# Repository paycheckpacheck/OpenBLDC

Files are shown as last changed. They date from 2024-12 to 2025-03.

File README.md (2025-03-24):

## Members
Pacheck Nicholas, Electrical Engineering Student (2025)
pacheck@vt.edu

Eddie Prichard (Computer Engineering Alum)

New contributors:
Enrico
Colton

## Mentor
Pacheck Nicholas
Eddie Prichard

## Current Status
IN PROGRESS

## Project Overview

The goal specifications for this motor driver should be to drive a 40V 10A load per phase. 

This project provides Open Source Hardware and Firmware for a 3-Phase Brushless DC Motor Driver. It aims to be an educational platform for some basic Power Electrionics problems.

To understand how a BLDC motor works, we must understand how a DC motor works. Well, its pretty simple, we apply a voltage and the motor spins. What if we want to have speed control? 
Well, we must decrease the average coil voltage. We can use a variable power supply to do this, or we can do this with a swith mode driver which will apply a PWM to the motor coil, allowing us to modify the duty cycle to compute the average voltage on the coil. 

An N-Channel Inverter is used to take that low power PWM generated from the discrete-controller/microcontroller and use it to switch on and off the Powersupply directly.

Below is an image of the N-Channel Inverter Developed after expirmental trials using a breadboard:



In additon to the cooresponding schematic:


This N-channel inverter essentially connects the Switch Node (Output) to power, or to ground. To Connect the Switch Node to Power, you must activate the High-Side Fet and deactivate the Low-side Fet; vice versa to connect to ground. 

But whats stopping us from just hooking up an inverter and directly driving the Gates of the Fets using something like an OpAmp? Gate Capacitance! In reality, there are two conditions required for a MOSFET to turn on ( Surpassing the Gate-Source voltage (VGS)) which is ussually found in the datasheet, AND filling up the gate capacitor. In order for a MOSFET to have fast switching, we must put consideration into the gate capacitance. In the datasheet, there is ussually like an effective gate charge, which is the total amount of charge needed to fill up the gate capacitor, this charge also needs to be dumped into the gate quicly, since there is a high frequrncy switching and not doing it fast enough or not filling it up entirely will cause the MOSFET to not fully turn on. 

Hence introducing the need for a bootstrap capacitor and bootstrap diode. These two components work as a team; the bootstrap diode allows the bootstrap capacitor to charge through the VCC, while also inuring the charge doesnt leak back in the way it came in. Now, during the lowside cycle, the bootstrap capacitor is charged up such that when the

The board has footprints for the 3-pin THT MOSFET package or the D-PACK6 Mosfet footprint.

A BLDC motor driver is just 3 of these. 


Here is the schem for the driver below.


## Educational Value Added
This BLDC driver is made out of primitive components. Instead of using a chip or IC which contains the entire BLDC driver, this project provides eduational value with the constraint that everything must be primitive. The current sense is done using a differential instrumentation amplifer made with op amps. Transient voltage supression (TVS) diodes are placed at the switch node with clamp voltage at about 32volts

## Tasks

<!-- Your Text Here. You may work with your mentor on this later when they are assigned -->

## Design Decisions

<!-- Your Text Here. You may work with your mentor on this later when they are assigned -->

## Steps for Documenting Your Design Process

<!-- Your Text Here. You may work with your mentor on this later when they are assigned -->

## BOM + Component Cost

<!-- Your Text Here. You may work with your mentor on this later when they are assigned -->

## Timeline

<!-- Your Text Here. You may work with your mentor on this later when they are assigned -->

## Useful Links

<!-- Your Text Here. You may work with your mentor on this later when they are assigned -->

## Log

<!-- Your Text Here. You may work with your mentor on this later when they are assigned -->

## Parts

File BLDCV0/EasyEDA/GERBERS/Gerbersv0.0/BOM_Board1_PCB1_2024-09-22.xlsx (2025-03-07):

No. | Quantity | Comment | Designator | Footprint | Value | Manufacturer Part | Manufacturer | Supplier Part | Supplier
1 | 9 | 0Ω | C1,C7,C13,C15,C16,C20,C22,C23,C27 | C0603 | 0Ω | RMC060301%N | Tyohm(幸亚电阻) | C269698 | LCSC
2 | 6 | 10uF | C9,C10,C17,C18,C24,C25 | CAP-SMD_BD5.0-L5.3-W5.3-LS6.3-FD | 10uF | RST10UF50V016 | KNSCHA(科尼盛) | C4747971 | LCSC
3 | 6 | 1uF | C12,C14,C19,C21,C26,C28 | CAP-TH_L7.2-W2.5-P5.00-D0.6 | 1uF | SMEC334J100M2 | CHAMPION(全鹏) |  | LCSC
4 | 3 | .1uF | C33,C34,C35 | C0402 | .1uF
5 | 1 | 500nF | C36 | C0603 | 500nF
6 | 1 | 1uF | C37 | CAP-SMD_BD5.0-L5.3-W5.3-LS6.3-FD | 1uF
7 | 1 | 200nF | C38 | C0603 | 200nF
8 | 1 | .1uF | C39 | CAP-SMD_BD5.0-L5.3-W5.3-LS6.3-FD | .1uF
9 | 3 | 1N5819WS | D1,D3,D5 | SOD-323_L1.8-W1.3-LS2.5-RD |  | 1N5819WS | Hottech(合科泰) | C191023 | LCSC
10 | 4 | P6SMB6.8CA/TR13 | D2,D4,D6,D8 | SMB_L4.6-W3.6-LS5.3-BI |  | P6SMB6.8CA/TR13 | Brightking(君耀电子) | C78395 | LCSC
11 | 1 | 1N4007 | D7 | DO-41_BD2.4-L4.7-P8.70-D0.9-RD
12 | 1 | HDR-F-2.54_2x2 | DGHTRPWR | HDR-TH_4P-P2.54-V-F-R2-C2-S2.54
13 | 2 | 2.54-1*6P母 | DRV_IN,SenseOut | HDR-TH_6P-P2.54-V-F |  | 2.54-1*6P母 | BOOMELE(博穆精密) | C40877 | LCSC
14 | 3 | HDR-M_2.54_1x4P | H1,H2,H3 | HDR-TH_4P-P2.54-V-M
15 | 1 | 1729128 | PWR_IN | CONN-TH_2P-P5.08 |  | 1729128 | Phoenix Contact(菲尼克斯) | C91153 | LCSC
16 | 6 | IRF2804STRL7PP | Q1,Q2,Q3,Q4,Q5,Q6 | D2PAK-7_L10.6-W9.6-P1.27-LS15.9-BR |  | IRF2804STRL7PP | Infineon(英飞凌) | C459950 | LCSC
17 | 3 | 5mΩ | R7,R10,R13 | R2512 | 5mΩ | PA2512FKF7W0R005E | YAGEO(国巨) | C309526 | LCSC
18 | 6 | 10kΩ | R8,R9,R11,R12,R14,R15 | RES-TH_BD3.3-L9.0-P13.00-D0.6 | 10kΩ
19 | 1 | 720 | R16 | RES-TH_BD3.3-L9.0-P13.00-D0.6 | 720
20 | 1 | 240 | R17 | RES-TH_BD3.3-L9.0-P13.00-D0.6 | 240
21 | 6 | 0Ω | RHS1,RHS2,RHS3,RLS1,RLS2,RLS3 | R1210 | 0Ω | SCR1210F0R | VO(翔胜) | C3017387 | LCSC
22 | 3 | IR2104PBF | U1,U2,U3 | DIP-8_L9.9-W6.6-P2.54-LS7.62-BL |  | IR2104PBF | Infineon(英飞凌) | C2959 | LCSC
23 | 3 | INA180A3IDBVT | U4,U5,U6 | SOT-23-5_L2.9-W1.6-P0.95-LS2.8-TL |  | INA180A3IDBVT | TI(德州仪器) | C2877844 | LCSC
24 | 1 | LM317T | U9 | TO-220-3_L10.0-W4.6-P2.54-L |  | LM317T | Siproin(上海矽朋) | C5444279 | LCSC
25 | 1 | XY636-7.62-3P | U10 | CONN-TH_XY636-7.62-3P |  | XY636-7.62-3P | XINLAIYA(新莱亚) | C880593 | LCSC

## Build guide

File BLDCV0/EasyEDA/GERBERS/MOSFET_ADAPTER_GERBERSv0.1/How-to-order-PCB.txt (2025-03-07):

How to Order PCB

Please refer to:
https://prodocs.easyeda.com/en/pcb/order-order-pcb/index.html

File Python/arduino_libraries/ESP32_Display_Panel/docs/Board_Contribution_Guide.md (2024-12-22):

# Board Contribution Guide

1. Newly added development boards must ensure the hardware schematics are open-source. Please provide a link or file.
2. This library currently only supports the APIs provided in ESP-IDF. It does not support other Arduino library APIs, such as Wire.

**Note**:
1. It is recommended to use the vscode + Arduino CLI development environment.
2. Pull the ESP32_Display_Panel repository into the Arduino library directory before making modifications.
3. The project uses pre-commit to enforce commit standards. It is recommended to install the pre-commit library before committing using the following command:

```
pip3 install pre-commit && pre-commit install
```

## Modification Content

Using the adaption of the [`M5Stack M5DIAL`](https://github.com/esp-arduino-libs/ESP32_Display_Panel/commit/1886c668468626b9dd2ae975f7db12df5413378e) development board as an example. Following this guide, changes below will be made under the project:

```
| -ESP32_Display_Panel
   | -src
      | -board
         | -m5stack                    [A]
            | -M5DIAL.h                [A]
         | -ESP_PanelBoard             [M]
         | -README.md                  [M]
      | -ESP_PanelVersions.h           [M]
   | -CHANGELOG.md                     [M]
   | -ESP_Panel_Board_Custom.h
   | -ESP_Panel_Board_Supported.h      [M]
   | -library.properties               [M]
   | -README_CN.md                     [M]
   | -README.md                        [M]
```
Note: [A] stands for 'append' and [M] stands for 'modify'

## Modification Process

Using the adaption of `M5Stack M5DIAL` as an example, follow these steps to modify the relevant files:

1. **[M]** *[ESP_Panel_Board_Supported.h](../ESP_Panel_Board_Supported.h)*: Add a macro for the new development board, such as `BOARD_M5STACK_M5DIAL`. Ensure the macro is in uppercase. Include the manufacturer's name and link, as well as the target development board's link.
2. **[A]** *[src/board/m5stack/M5DIAL.h](../src/board/m5stack/M5DIAL.h)*: Use the *ESP_Panel_Board_Custom.h* file in the root directory as a template to create a new configuration header file for the development board. Follow the naming conventions of existing development boards.
3. **[M]** *[src/board/ESP_PanelBoard.h](../src/board/ESP_PanelBoard.h)*: Add the macro check for the new development board by referring to the existing boards in the file, and modify the file to use the correct header file for this development board.

   **Note**: At this point, you can verify the above steps:

      - Choose an example, such as *[examples/Panel/PanelTest](../examples/Panel/PanelTest/)*.
      - modify the macro `ESP_PANEL_USE_SUPPORTED_BOARD` to enable this header file. Define the development board macro, such as `BOARD_M5STACK_M5DIAL`, to enable the new header file *[src/board/m5stack/M5DIAL.h](../src/board/m5stack/M5DIAL.h)*.
      - Verify the example's ino file. If successful, proceed to the following steps.

4. **[M]** *[src/board/m5stack/M5DIAL.h](../src/board/m5stack/M5DIAL.h)*: Modify the configuration header file for the new development board:
   - Review the hardware schematics of the development board, focusing on the BUS type used for the LCD screen, the LCD driver name, the BUS type used for touch, the touch driver name, and the chip pin numbers used for each interface of the LCD and touch.
   - The best practice is to first get the screen working, then work on the touch functionality.
   - If the new development board's driver is compatible with an existing driver, there is no need to add a new driver. Simply note in the comments that this driver is compatible with an existing one and use the existing driver.
   - If the driver used by the new development board is not compatible with existing drivers or has other special configurations, you can achieve this by modifying the macro functions at the end of the new development board's configuration header file, such as `ESP_PANEL_BEGIN_BACKLIGHT_START_FUNCTION`, `ESP_PANEL_BEGIN_END_FUNCTION`, etc. Refer to *[src/board/espressif/ESP32_S3_BOX_3.h](../src/board/espressif/ESP32_S3_BOX_3.h)* or *[src/board/m5stack/M5DIAL.h](../src/board/m5stack/M5DIAL.h)* for specific implementations.
   - Run examples other than *[examples/LCD](../examples/LCD/)* and *[examples/Touch](../examples/Touch/)*, and continuously adjust the configuration header file to ensure correct settings.

5. **[M]** *[ESP_Panel_Board_Supported](../ESP_Panel_Board_Supported.h)*, *[library.properties](../library.properties)*, *[docs/Board_Instructions.md](../docs/Board_Instructions.md)*, *[README_CN.md](../README_CN.md)*, *[README.md](../README.md)*: Update the supported development boards information in these files.
6. **[M]** *[docs/Board_Instructions.md](../docs/Board_Instructions.md)*: Update the recommended configuration for the new development board.
7. **[M]** *[src/ESP_PanelVersions.h](../src/ESP_PanelVersions.h)*: Ensure that the version under `Library Version` should be ahead of the latest tag version in terms of the tag version; when changes occur to *[ESP_Panel_Board_Custom.h](../ESP_Panel_Board_Custom.h)*, *[ESP_Panel_Board_Supported.h](../ESP_Panel_Board_Supported.h)*, and *[ESP_Panel_Conf.h](../ESP_Panel_Conf.h)* in the root directory, ensure that the version number at the end of the corresponding file and at the beginging of *[src/ESP_PanelVersions.h](../src/ESP_PanelVersions.h)* should be ahead of the latest tag version in terms of the minor version.
8. **[M]** *[CHANGELOG.md](../CHANGELOG.md)*: Update the changelog.

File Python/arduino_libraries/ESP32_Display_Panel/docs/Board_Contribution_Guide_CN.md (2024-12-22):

# 开发板贡献指南

1. 新添加的开发板需要确保硬件原理图开源，需要提供链接或文件。
2. 该库目前仅支持 ESP-IDF 提供的 API，不支持其他 Arduino 库 API，如 Wire。

**注意**：
1. 推荐使用 vscode + Arduino CLI 开发环境。
2. 在进行修改之前，将 ESP32_Display_Panel 仓库拉入 Arduino 库目录中。
3. 项目使用 pre-commit 来规范提交内容，因此建议在提交之前安装 pre-commit 库，使用以下命令：

```
pip3 install pre-commit && pre-commit install
```

## 需修改内容

以适配 [`M5Stack M5DIAL`](https://github.com/esp-arduino-libs/ESP32_Display_Panel/commit/1886c668468626b9dd2ae975f7db12df5413378e) 开发板为例。按照本指南，以下更改将在项目中进行：

```
| -ESP32_Display_Panel
   | -src
      | -board
         | -m5stack                    [A]
            | -M5DIAL.h                [A]
         | -ESP_PanelBoard             [M]
         | -README.md                  [M]
      | -ESP_PanelVersions.h           [M]
   | -CHANGELOG.md                     [M]
   | -ESP_Panel_Board_Custom.h
   | -ESP_Panel_Board_Supported.h      [M]
   | -library.properties               [M]
   | -README_CN.md                     [M]
   | -README.md                        [M]
```
注：[A] 代表 '添加'，[M] 代表 '修改'

## 各文件修改流程

以适配 `M5Stack M5DIAL` 为例，按照以下步骤修改相关文件：

1. **[M]** *[ESP_Panel_Board_Supported.h](../ESP_Panel_Board_Supported.h)*：为新开发板添加一个宏，例如 `BOARD_M5STACK_M5DIAL`。命名时注意宏名大写。注意附上开发板制造商的名称和链接，以及目标开发板的链接。
2. **[A]** *[src/board/m5stack/M5DIAL.h](../src/board/m5stack/M5DIAL.h)*：使用根目录中的 *ESP_Panel_Board_Custom.h* 文件作为模板，为开发板创建一个新的配置头文件。文件命名请参考已有开发板。
3. **[M]** *[src/board/ESP_PanelBoard.h](../src/board/ESP_PanelBoard.h)*：参照文件中其他开发板的写法，添加新开发板的宏名判断，并注意修改此开发板所使用的头文件。

   **注意**：此时，可以验证上述步骤：

      - 选择一个示例，例如 *[examples/Panel/PanelTest](../examples/Panel/PanelTest/)*。
      - 修改宏 `ESP_PANEL_USE_SUPPORTED_BOARD` 以启用此头文件。定义开发板宏，例如 `BOARD_M5STACK_M5DIAL`，以启用新的头文件 *[src/board/m5stack/M5DIAL.h](../src/board/m5stack/M5DIAL.h)*。
      - 验证示例的 ino 文件。如果成功，继续后续步骤。

4. **[M]** *[src/board/m5stack/M5DIAL.h](../src/board/m5stack/M5DIAL.h)*：修改新开发板的配置头文件：
   - 审查开发板的硬件原理图，重点关注LCD 屏幕所使用 BUS 类型、 LCD 驱动名、touch 所使用 BUS 类型、touch 驱动名，以及 LCD 和 touch 各接口所使用的芯片管脚号。
   - 修改技巧是先亮屏再 touch。
   - 如果新开发板的驱动程序与现有驱动程序兼容，则无需添加新驱动程序。只需在注释中注明该驱动程序与现有驱动程序兼容，并使用现有驱动程序。
   - 如果新开发板使用的驱动程序与现有驱动程序不兼容或有其他特殊配置，可以通过修改新开发板配置头文件末尾的宏函数来实现，例如 `ESP_PANEL_BEGIN_BACKLIGHT_START_FUNCTION`、`ESP_PANEL_BEGIN_END_FUNCTION` 等。具体实现请参考 *[src/board/espressif/ESP32_S3_BOX_3.h](../src/board/espressif/ESP32_S3_BOX_3.h)* 或 *[src/board/m5stack/M5DIAL.h](../src/board/m5stack/M5DIAL.h)*。
   - 运行除 *[examples/LCD](../examples/LCD/)* 和 *[examples/Touch](../examples/Touch/)* 以外的示例，并不断调整配置头文件以确保设置正确。

5. **[M]** *[ESP_Panel_Board_Supported](../ESP_Panel_Board_Supported.h)*、*[library.properties](../library.properties)*、*[docs/Board_Instructions.md](../docs/Board_Instructions.md)*、*[README_CN.md](../README_CN.md)*、*[README.md](../README.md)*：更新上述文件中“已支持开发板”说明。
6. **[M]** *[docs/Board_Instructions.md](../docs/Board_Instructions.md)*：更新新开发板的推荐配置。
7. **[M]** *[src/ESP_PanelVersions.h](../src/ESP_PanelVersions.h)*：确保 `Library Version` 下的版本应小版本领先于最新 tag 版本。当根目录下的 *[ESP_Panel_Board_Custom.h](../ESP_Panel_Board_Custom.h)*、*[ESP_Panel_Board_Supported.h](../ESP_Panel_Board_Supported.h)* 和 *[ESP_Panel_Conf.h](../ESP_Panel_Conf.h)* 发生变化时，相应文件末尾和 *[src/ESP_PanelVersions.h](../src/ESP_PanelVersions.h)* 开头的版本号应中版本领先于最新 tag 版本。
8. **[M]** *[CHANGELOG.md](../CHANGELOG.md)*：更新变更日志。

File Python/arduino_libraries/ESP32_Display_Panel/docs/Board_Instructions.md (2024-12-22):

# Board Instructions

## Internal Supported Development Boards

### [Espressif](https://www.espressif.com/en/products/devkits)

| **Picture** | **Name** | **LCD Bus** | **LCD Controller** | **LCD resolution** | **Touch Bus** | **Touch Controller** |
| :---: | :---: | :---: | :---: | :---: | :---: | :---: |
|  | [ESP32-C3-LCDkit](https://docs.espressif.com/projects/esp-dev-kits/en/latest/esp32c3/esp32-c3-lcdkit/index.html) | SPI | GC9A01 | 240x240 | - | - |
|  | [ESP32-S3-BOX](https://github.com/espressif/esp-box/tree/master) | SPI | ILI9342 | 320x240 | I2C | TT21100 |
|  | [ESP32-S3-BOX-3 & ESP32-S3-BOX-3B](https://github.com/espressif/esp-box/tree/master) | SPI | ILI9342 | 320x240 | I2C | GT911 |
|  | [ESP32-S3-BOX-3(beta)](https://github.com/espressif/esp-box/tree/c4c954888e11250423f083df0067d99e22d59fbe) | SPI | ILI9342 | 320x240 | I2C | TT21100 |
|  | [ESP32-S3-BOX-Lite](https://github.com/espressif/esp-box/tree/master) | SPI | ST7789 | 320x240 | - | - |
|  | [ESP32-S3-EYE](https://github.com/espressif/esp-who/blob/master/docs/en/get-started/ESP32-S3-EYE_Getting_Started_Guide.md) | SPI | ST7789 | 240x240 | - | - |
|  | [ESP32-S3-Korvo-2](https://docs.espressif.com/projects/esp-adf/en/latest/design-guide/dev-boards/user-guide-esp32-s3-korvo-2.html) | SPI | ILI9342 | 320x240 | I2C | TT21100 |
|  | [ESP32-S3-LCD-EV-Board](https://docs.espressif.com/projects/esp-dev-kits/en/latest/esp32s3/esp32-s3-lcd-ev-board/index.html) | 3-wire SPI + RGB | GC9503 | 480x480 | I2C | FT5x06 |
|  | [ESP32-S3-LCD-EV-Board-2](https://docs.espressif.com/projects/esp-dev-kits/en/latest/esp32s3/esp32-s3-lcd-ev-board/index.html) | RGB | ST7262E43 | 800x480 | I2C | GT1151 |
|  | [ESP32-S3-USB-OTG](https://docs.espressif.com/projects/esp-dev-kits/en/latest/esp32s3/esp32-s3-usb-otg/index.html) | SPI | ST7789 | 240x240 | - | - |

### [Elecrow](https://www.elecrow.com/)

| **Picture** | **Name** | **LCD Bus** | **LCD Controller** | **LCD resolution** | **Touch Bus** | **Touch Controller** |
| :---: | :---: | :---: | :---: | :---: | :---: | :---: |
|  | [CrowPanel 7.0"](https://www.elecrow.com/esp32-display-7-inch-hmi-display-rgb-tft-lcd-touch-screen-support-lvgl.html) | RGB | EK9716BD3 & EK73002ACGB | 800x480 | I2C | GT911 |

### [M5Stack](https://m5stack.com/)

| **Picture** | **Name** | **LCD Bus** | **LCD Controller** | **LCD resolution** | **Touch Bus** | **Touch Controller** |
| --- | --- | --- | --- | --- | --- | --- |
|  | [M5STACK_M5CORE2](https://docs.m5stack.com/en/core/core2) | SPI | ILI9342C | 320x240 | I2C | FT6336U |
|  | [M5STACK_M5DIAL](https://docs.m5stack.com/en/core/M5Dial) | SPI | GC9A01 | 240x240 | I2C | FT5x06 |
|  | [M5STACK_M5CORES3](https://docs.m5stack.com/en/core/CoreS3) | SPI | ILI9342C | 320x240 | I2C | FT6336U |

### [Shenzhen Jingcai Intelligent](https://www.displaysmodule.com/)

| **Picture** | **Name** | **LCD Bus** | **LCD Controller** | **LCD resolution** | **Touch Bus** | **Touch Controller** |
| :---: | :---: | :---: | :---: | :---: | :---: | :---: |
| [](https://www.displaysmodule.com/sale-41828962-experience-the-power-of-the-esp32-display-module-sku-esp32-4848s040c-i-y-3.html) | [ESP32-4848S040C_I_Y_3](http://pan.jczn1688.com/directlink/1/ESP32%20module/4.0inch_ESP32-4848S040.zip) | 3-wire SPI + RGB | ST7701 | 480x480 | I2C | GT911 |

## [Waveshare](https://www.waveshare.com/)

| **Picture** | **Name** | **LCD Bus** | **LCD Controller** | **LCD resolution** | **Touch Bus** | **Touch Controller** |
| :---: | :---: | :---: | :---: | --- | :---: | :---: |
|  | [ESP32-S3-Touch-LCD-4.3](https://www.waveshare.com/esp32-s3-touch-lcd-4.3.htm) | RGB | ST7262 | 800x480 | I2C | GT911 |

## Recommended Configurations in the Arduino IDE

Below are recommended configurations for developing GUI applications on different development boards. These settings can be adjusted according to specific requirements, and users can navigate to the `Tools` menu in the Arduino IDE to configure the following settings.

| Supported Boards | Selected Board |  PSRAM | Flash Mode | Flash Size | USB CDC On Boot | Partition Scheme |
| :---: | :---: | :---: | :---: | :---: | :---: | :---: |
| ESP32-C3-LCDkit | ESP32C3 Dev Module | Disabled | QIO | 4MB (32Mb) | Enabled | Default 4MB with spiffs |
| ESP32-S3-BOX | ESP32-S3-BOX | - | - | - | - | 16M Flash (3MB) |
| ESP32-S3-BOX-3 & ESP32-S3-BOX-3B | ESP32S3 Dev Module | OPI | QIO 80MHz  | 16MB | Enabled | 16M Flash (3MB) |
| ESP32-S3-BOX-3(beta) | ESP32S3 Dev Module | OPI | QIO 80MHz  | 16MB | Enabled | 16M Flash (3MB) |
| ESP32-S3-BOX-Lite | ESP32-S3-BOX | - | - | - | - | 16M Flash (3MB) |
| ESP32-S3-EYE | ESP32S3 Dev Module | OPI | QIO 80MHz  | 8MB | Enabled | 8M with spiffs |
| ESP32-S3-Korvo-2 | ESP32S3 Dev Module | OPI | QIO 80MHz  | 16MB | Disabled | 16M Flash (3MB) |
| ESP32-S3-LCD-EV-Board | ESP32S3 Dev Module | OPI | QIO 80MHz  | 16MB | **See Note 1**  | 16M Flash (3MB) |
| ESP32-S3-LCD-EV-Board-2 | ESP32S3 Dev Module | OPI | QIO 80MHz  | 16MB | **See Note 1**  | 16M Flash (3MB) |
| ESP32-S3-USB-OTG |  ESP32-S3-USB-OTG  | - | - | - | - | 8M with spiffs |
| M5STACK-M5CORE2 | M5Stack-Core2 | Enabled  | - | - | - | Default |
| M5STACK-M5DIAL | ESP32S3 Dev Module | OPI | QIO 80MHz  | 8MB | Disabled | Default |
| M5STACK-M5CORES3 | ESP32S3 Dev Module | OPI | QIO 80MHz  | 16MB | Enabled | Default 4MB with spiffs |
| ESP32-4848S040C_I_Y_3 | ESP32S3 Dev Module | OPI | QIO 80MHz  | 16MB | Disabled | 16M Flash (3MB) |
| ElecrowCrowPanel 7.0" | ESP32S3 Dev Module | OPI | QIO 80MHz  | 4MB | Disabled | Huge App (3MB) |
| Waveshare-ESP32-S3-Touch-LCD-4.3 | ESP32S3 Dev Module | OPI | QIO 80MHz  | 8MB | Disabled | 8M with spiffs |

**Notes:**

1. Enable or disable `USB CDC On Boot` based on the type of port used:

   * Disable this configuration if using **UART** port; enable it if using **USB** port.
   * If this configuration differs from previous flashing, first enable `Erase All Flash Before Sketch Upload`, then it can be disabled after flashing.
   * If this configuration does not match the actual port type, it will prevent the development board from printing serial logs correctly.

2. To view more output logs, set `Core Debug Level` to `Info` or a lower level.
3. If the predefined partition schemes provided by ESP32 do not meet the requirements, users can also select `Custom` in the "Partition Scheme" and create a custom partition table file `Custom.csv` in the `hardware/esp32/3.x.x/tools/partitions` directory under the [arduino-esp32 installation directory](#where-are-the-installation-directory-for-arduino-esp32-and-the-sdk-located). For detailed information on partition tables, please refer to the [ESP-IDF documentation](https://docs.espressif.com/projects/esp-idf/en/latest/esp32/api-guides/partition-tables.html).

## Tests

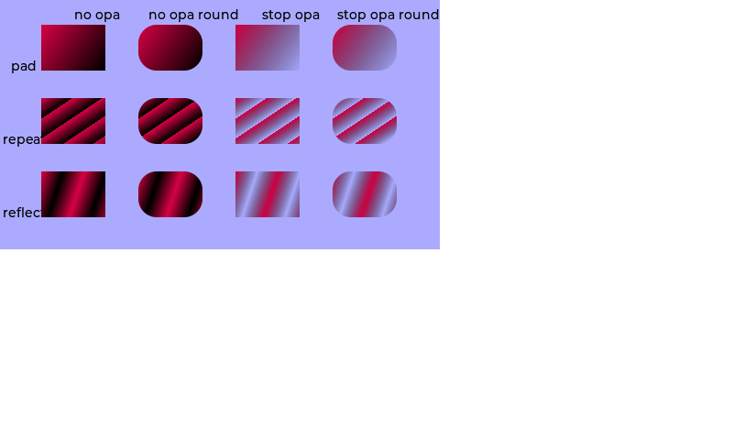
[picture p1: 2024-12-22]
Python/arduino_libraries/lvgl/tests/ref_imgs/draw/render/rgb565/demo_render_linear_gradient_opa_255.png

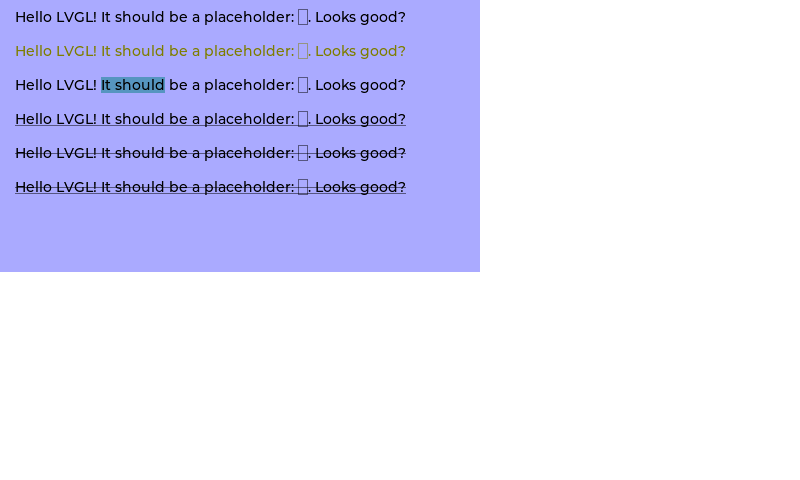
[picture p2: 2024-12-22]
Python/arduino_libraries/lvgl/tests/ref_imgs_vg_lite/draw/render/xrgb8888/demo_render_text_opa_128.png

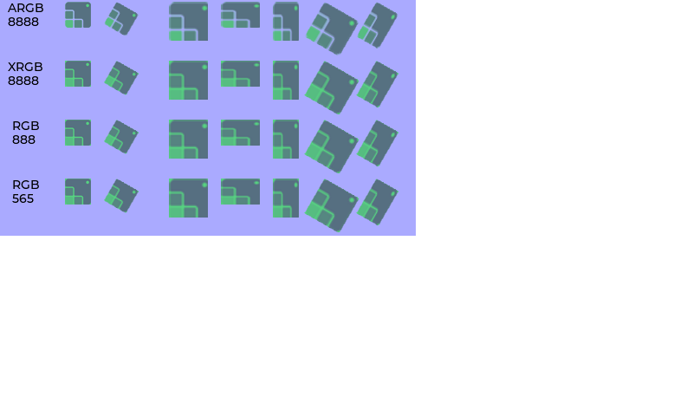
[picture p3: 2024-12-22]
Python/arduino_libraries/lvgl/tests/ref_imgs_vg_lite/draw/render/argb8888/demo_render_image_recolor_1_opa_255.png

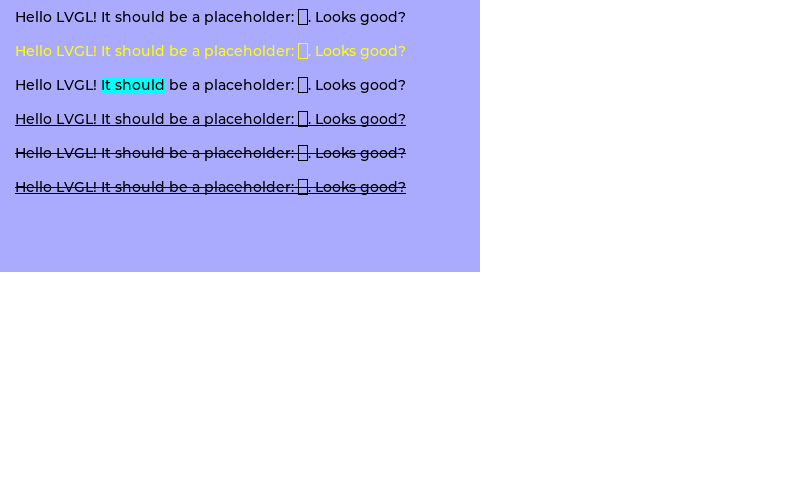
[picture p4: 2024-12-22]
Python/arduino_libraries/lvgl/tests/ref_imgs_vg_lite/draw/render/argb8888/demo_render_text_opa_255.png

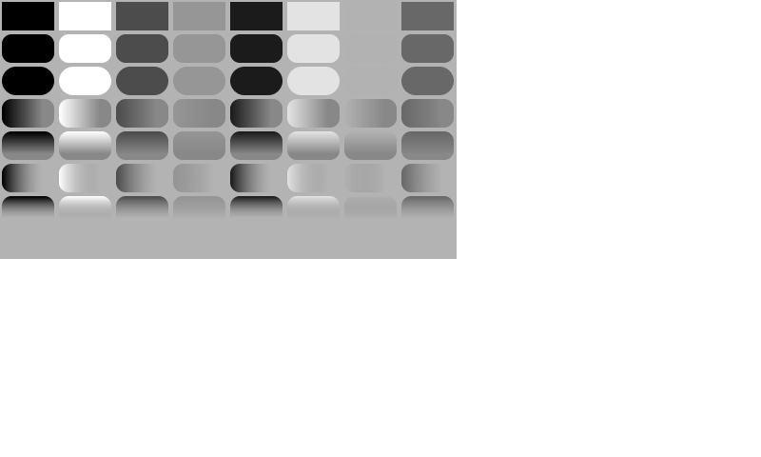
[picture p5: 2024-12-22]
Python/arduino_libraries/lvgl/tests/ref_imgs/draw/render/al88/demo_render_fill_opa_255.png

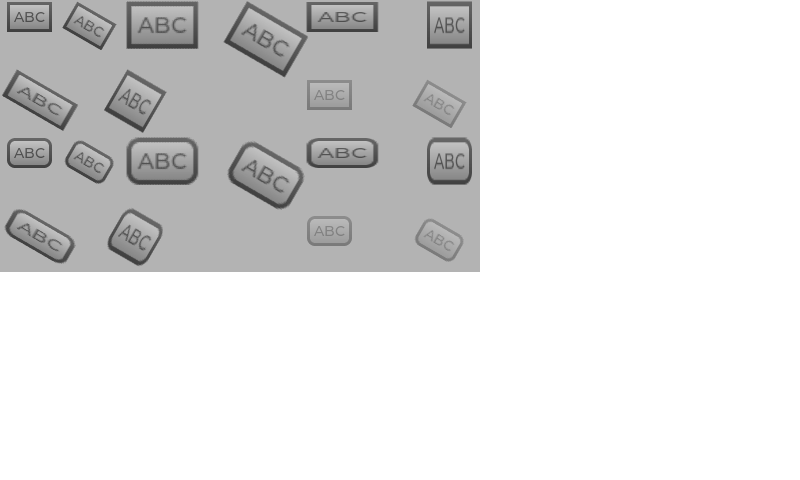
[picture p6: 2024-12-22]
Python/arduino_libraries/lvgl/tests/ref_imgs/draw/render/al88/demo_render_layer_normal_opa_128.png

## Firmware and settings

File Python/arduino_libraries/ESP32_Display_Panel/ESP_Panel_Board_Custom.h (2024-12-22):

/*
 * SPDX-FileCopyrightText: 2023-2024 Espressif Systems (Shanghai) CO LTD
 *
 * SPDX-License-Identifier: Apache-2.0
 */

#pragma once

// *INDENT-OFF*

/* Set to 1 if using a custom board */
#define ESP_PANEL_USE_CUSTOM_BOARD       (1)         // 0/1

#if ESP_PANEL_USE_CUSTOM_BOARD

////////////////////////////////////////////////////////////////////////////////////////////////////////////////////////
//////////////////////////// Please update the following macros to configure the LCD panel /////////////////////////////
////////////////////////////////////////////////////////////////////////////////////////////////////////////////////////
/* Set to 1 when using an LCD panel */
#define ESP_PANEL_USE_LCD           (1)     // 0/1

#if ESP_PANEL_USE_LCD
/**
 * LCD Controller Name. Choose one of the following:
 *      - EK9716B
 *      - GC9A01, GC9B71, GC9503
 *      - ILI9341
 *      - NV3022B
 *      - SH8601
 *      - SPD2010
 *      - ST7262, ST7701, ST7789, ST7796, ST77916, ST77922
 */
#define ESP_PANEL_LCD_NAME          ST7789

/* LCD resolution in pixels */
#define ESP_PANEL_LCD_WIDTH         (240)
#define ESP_PANEL_LCD_HEIGHT        (280)

/* LCD Bus Settings */
/**
 * If set to 1, the bus will skip to initialize the corresponding host. Users need to initialize the host in advance.
 * It is useful if other devices use the same host. Please ensure that the host is initialized only once.
 *
 * Set to 1 if only the RGB interface is used without the 3-wire SPI interface,
 */
#define ESP_PANEL_LCD_BUS_SKIP_INIT_HOST    (0)     // 0/1
/**
 * LCD Bus Type. Choose one of the following:
 *      - ESP_PANEL_BUS_TYPE_I2C (not ready)
 *      - ESP_PANEL_BUS_TYPE_SPI
 *      - ESP_PANEL_BUS_TYPE_QSPI
 *      - ESP_PANEL_BUS_TYPE_I80 (not ready)
 *      - ESP_PANEL_BUS_TYPE_RGB (only supported for ESP32-S3)
 */
#define ESP_PANEL_LCD_BUS_TYPE      (ESP_PANEL_BUS_TYPE_SPI)
/**
 * LCD Bus Parameters.
 *
 * Please refer to https://docs.espressif.com/projects/esp-idf/en/latest/esp32s3/api-reference/peripherals/lcd.html and
 * https://docs.espressif.com/projects/esp-iot-solution/en/latest/display/lcd/index.html for more details.
 *
 */
#if ESP_PANEL_LCD_BUS_TYPE == ESP_PANEL_BUS_TYPE_SPI

    #define ESP_PANEL_LCD_BUS_HOST_ID           (1)     // Typically set to 1
    #define ESP_PANEL_LCD_SPI_IO_CS             (5)
#if !ESP_PANEL_LCD_BUS_SKIP_INIT_HOST
    #define ESP_PANEL_LCD_SPI_IO_SCK            (7)
    #define ESP_PANEL_LCD_SPI_IO_MOSI           (6)
    #define ESP_PANEL_LCD_SPI_IO_MISO           (-1)    // -1 if not used
#endif
    #define ESP_PANEL_LCD_SPI_IO_DC             (4)
    #define ESP_PANEL_LCD_SPI_MODE              (0)     // 0/1/2/3, typically set to 0
    #define ESP_PANEL_LCD_SPI_CLK_HZ            (40 * 1000 * 1000)
                                                        // Should be an integer divisor of 80M, typically set to 40M
    #define ESP_PANEL_LCD_SPI_TRANS_QUEUE_SZ    (10)    // Typically set to 10
    #define ESP_PANEL_LCD_SPI_CMD_BITS          (8)     // Typically set to 8
    #define ESP_PANEL_LCD_SPI_PARAM_BITS        (8)     // Typically set to 8

#elif ESP_PANEL_LCD_BUS_TYPE == ESP_PANEL_BUS_TYPE_QSPI

    #define ESP_PANEL_LCD_BUS_HOST_ID           (1)     // Typically set to 1
    #define ESP_PANEL_LCD_SPI_IO_CS             (5)
#if !ESP_PANEL_LCD_BUS_SKIP_INIT_HOST
    #define ESP_PANEL_LCD_SPI_IO_SCK            (9)
    #define ESP_PANEL_LCD_SPI_IO_DATA0          (10)
    #define ESP_PANEL_LCD_SPI_IO_DATA1          (11)
    #define ESP_PANEL_LCD_SPI_IO_DATA2          (12)
    #define ESP_PANEL_LCD_SPI_IO_DATA3          (13)
#endif
    #define ESP_PANEL_LCD_SPI_MODE              (0)     // 0/1/2/3, typically set to 0
    #define ESP_PANEL_LCD_SPI_CLK_HZ            (40 * 1000 * 1000)
                                                        // Should be an integer divisor of 80M, typically set to 40M
    #define ESP_PANEL_LCD_SPI_TRANS_QUEUE_SZ    (10)    // Typically set to 10
    #define ESP_PANEL_LCD_SPI_CMD_BITS          (32)    // Typically set to 32
    #define ESP_PANEL_LCD_SPI_PARAM_BITS        (8)     // Typically set to 8
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

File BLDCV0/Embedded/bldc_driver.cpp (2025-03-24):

#include "bldc_driver.hpp"

// Phase class implementation
Phase::Phase(uint8_t hin, uint8_t sd, uint8_t cur) 
    : hinPin(hin)
    , sdPin(sd)
    , currentPin(cur)
    , pwmDuty(0)
    , current(0) {
    // Configure pins
    pinMode(hinPin, OUTPUT);
    pinMode(sdPin, OUTPUT);
    pinMode(currentPin, INPUT);
    disableOutput();
}

void Phase::setPWM(uint16_t duty) {
    pwmDuty = duty;
    analogWrite(hinPin, duty);
}

void Phase::enableOutput() {
    digitalWrite(sdPin, HIGH);  // Release shutdown
}

void Phase::disableOutput() {
    digitalWrite(sdPin, LOW);   // Assert shutdown
    setPWM(0);
}

void Phase::shutdown() {
    disableOutput();
}

void Phase::release() {
    enableOutput();
}

uint16_t Phase::readCurrent() {
    current = analogRead(currentPin);
    return current;
}

// BLDCDriver class implementation
BLDCDriver::BLDCDriver(uint8_t hinA, uint8_t sdA, uint8_t curA,
                       uint8_t hinB, uint8_t sdB, uint8_t curB,
                       uint8_t hinC, uint8_t sdC, uint8_t curC)
    : phaseA(hinA, sdA, curA)
    , phaseB(hinB, sdB, curB)
    , phaseC(hinC, sdC, curC)
    , currentStep(CommutationStep::STEP1)
    , motorSpeed(0)
    , isRunning(false)
    , overcurrentThreshold(900) {  // Default threshold, can be adjusted
}

void BLDCDriver::begin() {
    initADC();
    initPWM();
    
    // Ensure all phases are disabled at start
    phaseA.disableOutput();
    phaseB.disableOutput();
    phaseC.disableOutput();
}

void BLDCDriver::initADC() {
    // Configure ADC for current sensing
    analogReference(DEFAULT);
    // Perform dummy reads to initialize ADCs
    phaseA.readCurrent();
    phaseB.readCurrent();
    phaseC.readCurrent();
}

void BLDCDriver::initPWM() {
    // Configure PWM frequency and resolution
    // This will depend on your specific microcontroller
    // Example for Arduino:
    // TCCR1B = TCCR1B & B11111000 | B00000001; // Set PWM frequency to 31372.55 Hz
}

void BLDCDriver::setSpeed(uint16_t speed) {
    motorSpeed = speed;
    if (isRunning) {
        updateCommutation();
    }
}

void BLDCDriver::start() {
    if (!isRunning) {
        isRunning = true;
        currentStep = CommutationStep::STEP1;
        phaseA.release();
        phaseB.release();
        phaseC.release();
        updateCommutation();
    }
}

void BLDCDriver::stop() {
    isRunning = false;
    phaseA.disableOutput();
    phaseB.disableOutput();
    phaseC.disableOutput();
}

BLDCDriver::PhaseCurrent BLDCDriver::getCurrents() {
    return {
        phaseA.readCurrent(),
        phaseB.readCurrent(),
        phaseC.readCurrent()
    };
}

bool BLDCDriver::isOverCurrent() {
    auto currents = getCurrents();
    return (currents.phaseA > overcurrentThreshold ||
            currents.phaseB > overcurrentThreshold ||
            currents.phaseC > overcurrentThreshold);
}

void BLDCDriver::setOvercurrentThreshold(uint16_t threshold) {
    overcurrentThreshold = threshold;
}

void BLDCDriver::commutate() {
    if (!isRunning) return;
    
    // Advance to next commutation step
    currentStep = static_cast<CommutationStep>((static_cast<int>(currentStep) + 1) % 6);
    updateCommutation();
}

void BLDCDriver::updateCommutation() {
    // Standard 6-step commutation sequence
    switch (currentStep) {
        case CommutationStep::STEP1: // A-B
            phaseA.setPWM(motorSpeed);
            phaseB.setPWM(0);
            phaseC.disableOutput();
            break;
            
        case CommutationStep::STEP2: // A-C
            phaseA.setPWM(motorSpeed);
            phaseB.disableOutput();
            phaseC.setPWM(0);
            break;
            
        case CommutationStep::STEP3: // B-C
            phaseA.disableOutput();
            phaseB.setPWM(motorSpeed);
            phaseC.setPWM(0);
            break;
            
        case CommutationStep::STEP4: // B-A
            phaseA.setPWM(0);
            phaseB.setPWM(motorSpeed);
            phaseC.disableOutput();
            break;
            
        case CommutationStep::STEP5: // C-A
            phaseA.setPWM(0);
            phaseB.disableOutput();
            phaseC.setPWM(motorSpeed);
            break;
            
        case CommutationStep::STEP6: // C-B
            phaseA.disableOutput();
            phaseB.setPWM(0);
            phaseC.setPWM(motorSpeed);
            break;
    }
} 

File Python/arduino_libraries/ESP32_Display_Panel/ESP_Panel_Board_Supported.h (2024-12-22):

/*
 * SPDX-FileCopyrightText: 2023-2024 Espressif Systems (Shanghai) CO LTD
 *
 * SPDX-License-Identifier: Apache-2.0
 */

#pragma once

/* Set to 1 if using a supported board */
#define ESP_PANEL_USE_SUPPORTED_BOARD       (0)         // 0/1

#if ESP_PANEL_USE_SUPPORTED_BOARD 
/**
 * Uncomment one of the following macros to select an supported development board. If multiple macros are uncommented
 * at the same time, an error will be prompted during compilation.
 *
 */

/*
 * Espressif Supported Boards (https://www.espressif.com/en/products/devkits):
 *
 *  - BOARD_ESP32_C3_LCDKIT (ESP32-C3-LCDkit): https://docs.espressif.com/projects/esp-dev-kits/en/latest/esp32c3/esp32-c3-lcdkit/index.html
 *  - BOARD_ESP32_S3_BOX (ESP32-S3-Box): https://github.com/espressif/esp-box/tree/master
 *  - BOARD_ESP32_S3_BOX_3 (ESP32-S3-Box-3 & ESP32-S3-Box-3B): https://github.com/espressif/esp-box/tree/master
 *  - BOARD_ESP32_S3_BOX_3_BETA (ESP32-S3-Box-3(beta)): https://github.com/espressif/esp-box/tree/c4c954888e11250423f083df0067d99e22d59fbe
 *  - BOARD_ESP32_S3_BOX_LITE (ESP32-S3-Box-Lite): https://github.com/espressif/esp-box/tree/master
 *  - BOARD_ESP32_S3_EYE (ESP32-S3-EYE): https://github.com/espressif/esp-who/blob/master/docs/en/get-started/ESP32-S3-EYE_Getting_Started_Guide.md
 *  - BOARD_ESP32_S3_KORVO_2 (ESP32-S3-Korvo-2): https://docs.espressif.com/projects/esp-adf/en/latest/design-guide/dev-boards/user-guide-esp32-s3-korvo-2.html
 *  - BOARD_ESP32_S3_LCD_EV_BOARD (ESP32-S3-LCD-EV-Board): https://docs.espressif.com/projects/esp-dev-kits/en/latest/esp32s3/esp32-s3-lcd-ev-board/user_guide_v1.4.html
 *  - BOARD_ESP32_S3_LCD_EV_BOARD_V1_5 (ESP32-S3-LCD-EV-Board(v1.5)): https://docs.espressif.com/projects/esp-dev-kits/en/latest/esp32s3/esp32-s3-lcd-ev-board/user_guide.html
 *  - BOARD_ESP32_S3_LCD_EV_BOARD_2 (ESP32-S3-LCD-EV-Board-2)): https://docs.espressif.com/projects/esp-dev-kits/en/latest/esp32s3/esp32-s3-lcd-ev-board/user_guide_v1.4.html
 *  - BOARD_ESP32_S3_LCD_EV_BOARD_2_V1_5 (ESP32-S3-LCD-EV-Board-2(v1.5)): https://docs.espressif.com/projects/esp-dev-kits/en/latest/esp32s3/esp32-s3-lcd-ev-board/user_guide.html
 *  - BOARD_ESP32_S3_USB_OTG (ESP32-S3-USB-OTG): https://docs.espressif.com/projects/esp-dev-kits/en/latest/esp32s3/esp32-s3-usb-otg/index.html
 *
 */
// #define BOARD_ESP32_C3_LCDKIT
// #define BOARD_ESP32_S3_BOX
// #define BOARD_ESP32_S3_BOX_3
// #define BOARD_ESP32_S3_BOX_3_BETA
// #define BOARD_ESP32_S3_BOX_LITE
// #define BOARD_ESP32_S3_EYE
// #define BOARD_ESP32_S3_KORVO_2
// #define BOARD_ESP32_S3_LCD_EV_BOARD
// #define BOARD_ESP32_S3_LCD_EV_BOARD_V1_5
// #define BOARD_ESP32_S3_LCD_EV_BOARD_2
// #define BOARD_ESP32_S3_LCD_EV_BOARD_2_V1_5
// #define BOARD_ESP32_S3_USB_OTG

/*
 * Elecrow (https://www.elecrow.com):
 *
 *  - BOARD_ELECROW_CROWPANEL_7_0 (ELECROW_CROWPANEL_7_0): https://www.elecrow.com/esp32-display-7-inch-hmi-display-rgb-tft-lcd-touch-screen-support-lvgl.html
 */
// #define BOARD_ELECROW_CROWPANEL_7_0

/*
 * M5Stack (https://m5stack.com/):
 *
 *  - BOARD_M5STACK_M5CORE2 (M5STACK_M5CORE2): https://docs.m5stack.com/zh_CN/core/core2
 *  - BOARD_M5STACK_M5DIAL (M5STACK_M5DIAL): https://docs.m5stack.com/zh_CN/core/M5Dial
 *  - BOARD_M5STACK_M5CORES3 (M5STACK_M5CORES3): https://docs.m5stack.com/zh_CN/core/CoreS3
 */
// #define BOARD_M5STACK_M5CORE2
// #define BOARD_M5STACK_M5DIAL
// #define BOARD_M5STACK_M5CORES3

/*
 * Shenzhen Jingcai Intelligent Supported Boards (https://www.displaysmodule.com/):
 *
 *  - BOARD_ESP32_4848S040C_I_Y_3 (ESP32-4848S040C_I_Y_3):
 *      - https://www.displaysmodule.com/sale-41828962-experience-the-power-of-the-esp32-display-module-sku-esp32-4848s040c-i-y-3.html
 *      - http://pan.jczn1688.com/directlink/1/ESP32%20module/4.0inch_ESP32-4848S040.zip
 *
 */
// #define BOARD_ESP32_4848S040C_I_Y_3

/*
 * Waveshare Supported Boards (https://www.waveshare.com/):
 *
 *  - ESP32_S3_Touch_LCD_4_3:
 *      - https://www.waveshare.com/esp32-s3-touch-lcd-4.3.htm
 *
 */
// #define BOARD_WAVESHARE_ESP32_S3_Touch_LCD_4_3
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

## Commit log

2025-03-07 Added Project Files
    [BOM_Board1_PCB1_2024-09-22.xlsx, BOM_Board1_PCB1_2024-09-25.xlsx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]
2025-03-22 Added current sense block in BLDCV5
